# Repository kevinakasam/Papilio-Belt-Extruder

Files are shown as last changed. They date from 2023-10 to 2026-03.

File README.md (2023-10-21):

# Papilio-Belt-Extruder



#### I recommend visiting my website for slightly more aesthetic documentation :)

## A Belt-Extruder, what is that?

No metal teeth biting the filament, but soft rubber belts pushing the filament down to the nozzle. This is the concept of the Papilio: A Belt Extruder which uses regular rubber timing belts instead of metal extruder gears to feed the filament.

You may wonder why we need an extruder that uses belts instead of gears? Guess it’s fair to say, that we all know the woodpattern on flat surfaces or the small bites on the filament when the metal gears grab the filament. With the belts there are no metal teeth damaging the filament, but soft rubber belts pressing against the filament guiding it all the way through the extruder into the nozzle. As all my projects the Papilio is an 100% opensource project.

 

## How does it work?

Powered by a Nema 14 the Papilio uses a gear reduction to drive two tiny 2GT looped timing belts. In order to keep everything as minimalistic and cheap as possible the Papilio uses very common hardware in combination with some printed parts. The Nema 14 doesn’t make it only super compact but also very light weight – only 140g!

The Papilio uses a Dual-Drive System so the filament gets pushed on both sides by the two timing belts. Using some special shaped pulleys the belts get curved and can perfectly warp around the filament. This ensures a maximum contact to the filament for a very strong grip and keep the filament centered.

## There are two of them?

Yes indeed! There are two versions of the extruder, the Papilio and Papilio Lite. After many many iterations the Papilio was the first working version of the belt extruder. The design reminded me on a butterfly so I named the extruder Papilio– latin for butterfly. But I didn’t stop! My goal was to develop a much more powerful design, so I went further into the rabbit hole. After many attempts and failures I ended up with the Papilio Lite: Less weight, more power. This doesn’t mean the original Papilio is outdated, he just got a brother.

 

## What has changed?

### The Papilio Lite

The Papilio Lite got it’s name from the it’s internals – rather than using the BMG Drive Gear assembly, the Lite uses the Gears from the LGX Lite. With the two stage reduction of 44:10 and 37:17 ( or 44:8, 37:17 with a 8T motor) the Papilio Lite is not only much stronger but also lighter! With 130g the Lite saves you another 10g on the toolhead compared to the original Papilio!

The Papilio Lite also uses a Dual-Drive System to feed the filament on both sides by the two timing belts. The much more closed design of the Papilio Lite allows you to print flexibles, which wasn’t possible with the original design.

Like the original Papilio, the Papilio Lite uses the Sherpa Mini footprint, making it compatible with a wide range of toolheads – due to it’s increased depth it got some additional mounting points lining up with the LGX Lite. The boxed and compact design makes it even compatible with the Voron Steathburner!



## Open source - this is our project!

As all my work the Papilio is also an Open Source project - all files are free to use! You get all the STLs and CAD files via my GitHub and the build logs below. I also added a User Mod Folder to the GitHub so you can contribute to the project with your awesome ideas and adaptions. I can't wait to see what you will come up with :) This extruder deserves it to be something special!

Also the CAD file is 100% parametric, so small adaptions like tolerances, different bearing or heatinserts sizes etc. are easy to do! I tried my best to describe the parameters, if you still have any questions feel free to ask. Ah and if you can't do CAD yourself, I'm sure I can help you out ;)



### ❤️ Support my work

All my work is 100% Open-Source and free for everyone to use. But designing and developing all these things takes a lot of time and effort, so if you appreciate my work and would like to support it and also help cover the costs of gettings the mods perfect, you can use one of the following links. Thanks a lot 🤍

<a href="https://www.buymeacoffee.com/kevinakasam" target="_blank">Buy Me A Coffee</a>


## How can I try this out?

### Current state: Beta-Testing

After seven months of a closed Alpha Testing it's time for a public Beta!

While we did a lot of testing and improving during the Alpha, there's still room for improvements. If the Papilio caught your interest you can now build your very own Papilio extruder! As for all my Beta testings all communication will happen on my Discord - check the channel "#papilio-chat" for more information. All files are available on my GitHub - check the build instructions below. 
Click on the icon to join my [Discord Server](https://discord.gg/xqpKrxt9FC):

<a href="https://discord.gg/xqpKrxt9FC">
         <img alt="Join" src="https://github.com/kevinakasam/BeltDrivenEnder3/blob/main/_ignore/Pictures/Discord-Logo%2BWordmark-Color.png"
         width=250" >
      </a>

### Alpha Testing: Completed

You are awesome! After half a year of Alpha testing we can now start the public Beta. Thank you very very much for all your help, suggestions, time and willing to help.  Shoutout to these awesome people:

You | are | some | really | awesome | People!!
:-------------------------: | :-------------------------: | :-------------------------: | :-------------------------: | :-------------------------: | :-------------------------:
 |   |   |   |   |      
1957Axel | 10Boltoa | aid3nn | André | Andy | barnus84
bigbosshogg412 | Bomble_doodle | Butter202 | Chilly | chestwood96 | [CR3D](https://www.cr3d.de/)
Ciccius | diabolicaldan | Farva | Fruitz | hawk16zz | interitus
JamesH | Keh | Kingn00dles | Lemcott | Luigivaba | macuser_1984
memy | Mr ed | Naraki | [oldcrazyeye/CrazyLlamaCustoms](https://github.com/oldcrazyeye) | oliof | PCR
Phanzer | PigeonGiraffe | pnewb | q66 | qwib | SpitefulOwl
Stu | tcbp | Tkaus | verm | Wight555 | [zruncho](https://github.com/zruncho3d)

## Build Instructions

I'm glad that you want to give the Papilio a try. Just click on the Papilio you want to build:

<a href="https://kevinakasam.com/papilio-build-instructions/">
         Click
      </a>

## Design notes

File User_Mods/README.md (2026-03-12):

# User Mods

This respository is to share your Mods (Mods of my Mods are called Mods in the following). You can add them by submitting a pullrequest.
All my Mods have a sperate folder, that may include further subfolders, please sort your content as described below:

## Table structure

*Thanks to the [Voron_User](https://github.com/VoronDesign/VoronUsers) Repo for this table shematic! 
Update the following table with the information about your mod:
- Your name
- A link to your sub-folder
- A short description of your mod
- The extruder compatibility. Use `:heavy_check_mark:` for :heavy_check_mark:,`:x:` for :x: and `:grey_question:` for :grey_question:

like so:
`
| Creator | [Mod title](link) | Description | :x: | :x: |`

| Creator | Mod title | Description | Papilio | Papilio Lite |
| --- | --- | --- | --- | --- |
| KevinAkaSam |[XOL2_Mounts](./KevinAkaSam/XOL2_Mounts)| XOL2 Mounts for the Papilio (Lite) including Tap  | :heavy_check_mark: | :heavy_check_mark: |
|  |[Stealthburner_Mount](./KevinAkaSam/Stealthburner_Mount)| Stealthburner Mount for the Papilio Lite  | :x: | :heavy_check_mark: |
| adamstorm | [Filament Sensors](./adamstorm/Filament%20Sensors) | Top Cover with filament sensors | :x: | :heavy_check_mark: |
| cobre | [A4T Extruder Adapters](./cobre/A4T%20Extruder%20Adapters) | Adapter to use Papilio extruder with A4T toolhead | :grey_question: | :heavy_check_mark: |
| hawk16zz | [PapLite Combo Mount](./hawk16zz/Combo_SM_LGX_lite_for_Frank2.0) | Extra mounting options for the PapLite with Frank2.0 | :x: | :heavy_check_mark: |
|  | [PapLite Strain Relief](./hawk16zz/Mountable_LGX_Lite_strain_relief) | Cable Strain Relief Bracket for PapLite | :x: | :heavy_check_mark: |
|  | [PapLite Front EBB36](./hawk16zz/Front_EBB36_PapLite) | Mount to attach a EBB36 to the Front of the PapLite | :x: | :heavy_check_mark: |
| n4t3 | [Papilio Top Cover HGX Collet](./n4t3/Papilio_HGX_Collet) | Top Cover to attach HGX Collet to top | :x: | :heavy_check_mark: |
|  | [Papilio Top Cover M6 Bowden Dual](./n4t3/Papilio_M6_Bowden_Dual) | Top Cover to attach M6 Bowden Coupler to top and bottom | :x: | :heavy_check_mark: |
|  | [Papilio Top Cover M6 Bowden](./n4t3/Papilio_M6_Bowden) | Top Cover to attach M6 Bowden Coupler to top | :x: | :heavy_check_mark: |
| theFPVgeek | [FlexiPap](./theFPVgeek/FlexiPap) | Modified Papilio Lite TPU Cover and HGX 1.x geared Upper Base for <95A flexible filaments | :x: | :heavy_check_mark: |

## How to create a pull request 

1. Create a fork of the respository
    - You can find a Button labeled `Fork` at the top right. Clinking on that creates a copy aka fork of this respository in your GitHub account.

2. Create a new folder
    - Navigate into the Mod folder you want to upload your Mod to.
    - Click on `Add file` -> `Create new file`. Then type `YourNickname/YourModName/README.md` to create your folder (click on `commit new file`).
    - If you plan to upload more than one Mod, add simply add more subfolders in your folder like `YourNickname/YourFirstModName/README.md` and `YourNickname/YourSecondModName/README.md` and so on. 
    - Please use short folder names.

3. Edit README and add your files
    - Click on the README.md and then on the pencil on the right top/center to edit the README. Add all required information as described below.
    - Click on `Add file` -> `Upload files` to upload all your Mod files.
    - The stock title of a commit is `Add files via upload` replace that with the title of your Mod.

4. Edit the main README.md of the Mod
    - Navigate back to the Mod folder you made your Mod for. Edit this file and add your mod to the alphabetic table by adding a new line with `| Creator | [Mod title](link) | Description | | :x: | :x: |`
    - The `link` for the `[Mod title](link)` should look like that: `./YourNickname/YourModName` just like you did above
    - Example: `| KevinAkaSam | [Modifius](./KevinAkaSam/Modifius) | Modifius adds ...  | :grey_question: | :grey_question: |`
    - Note `Modifius` is just an idea, yours may be called `Adaption to bearing size xy`

5. Submit the Pullrequest
    - Navigate back to this respository (not the one you forked) and click on `Pull requests` next to `<> Code` `© Issues`
    - Click on the green square on the right `New pull request`
    - A new dialog/window opens and starts with:
        >Compare changes
        >
        >Compare changes across branches, commits, tags, and more below. If you need to, you can also `compare across forks`.
    - Click on the `compare across forks` and at the line below select your forked respository as `head respository`
    - Add you Mod name as title of the pullrequest, add the information to the form and click on  `Create Pull Request` at the very end.
    - If you did anything right we will merge your pullrequest :)
 
## Create a folder

To add your work create a folder that has the following structure:

    - Main respository `User-Mods` 
        - Nickname Subfolder eg. `KevinAkaSam`
            - Modname Subfolder eg. `Modifius`
            - Modname Subfolder eg. `Modimedi`
        - Nickname Subfolder eg. `SamAkaKevin`
            - Modname Subfolder eg. `Mod_A`
            - Modname Subfolder eg. `Mod_B`

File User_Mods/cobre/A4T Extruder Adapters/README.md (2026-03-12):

# A4T Papilio Extruder Adapter

A new toolhead that seems to be gaining popularity is [Armchair Engineering's A4T](https://github.com/Armchair-Heavy-Industries/A4T/). I decided I was going to try it out, but I realized that my extruder wasn't going to fit. I recently switched to [KevinAkaSam's Papilio Lite](https://kevinakasam.com/papilio/) extruder, and while it uses the same mounting holes as Sherpa Mini (Which A4T supports without an extruder adapter), the stepper motor on the rear won't clear the toolhead cowl.

I remixed the included adapter for LGX Lite, and made versions for both XOL and CW2/Tap carriages. 

I have not tested this with Papilio non-lite, but I don't see why it wouldn't work

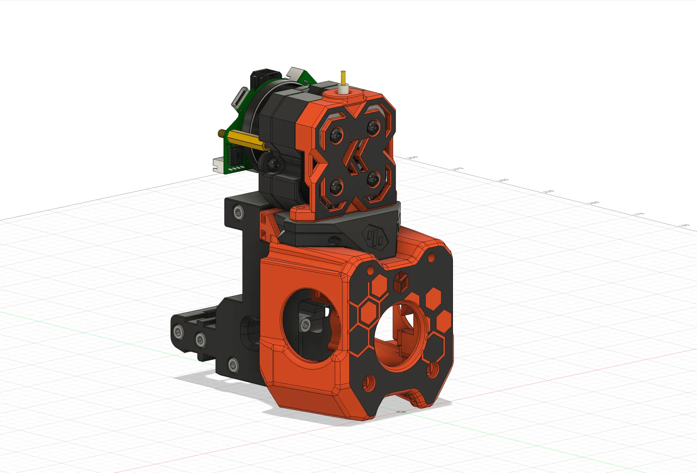
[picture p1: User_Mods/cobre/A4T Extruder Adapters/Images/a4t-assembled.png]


There are versions for both XOL and CW2/Tap carriages, and each has a variant with or without the Voron logo

<br>

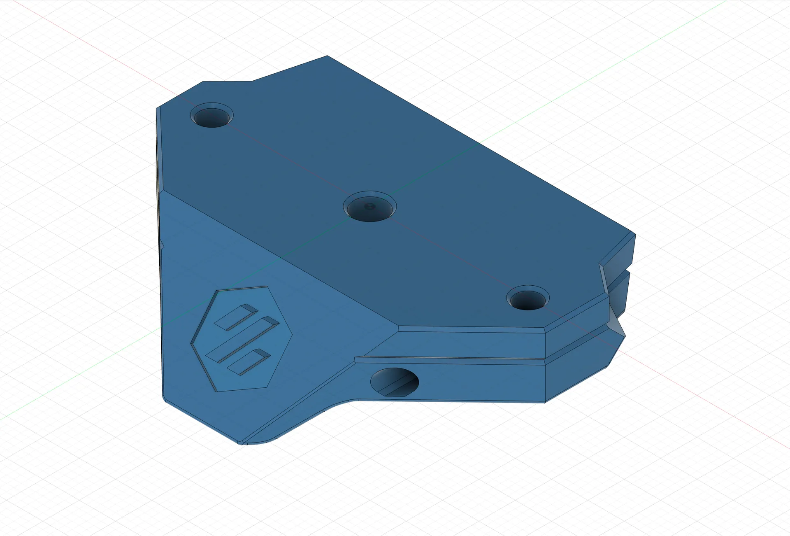
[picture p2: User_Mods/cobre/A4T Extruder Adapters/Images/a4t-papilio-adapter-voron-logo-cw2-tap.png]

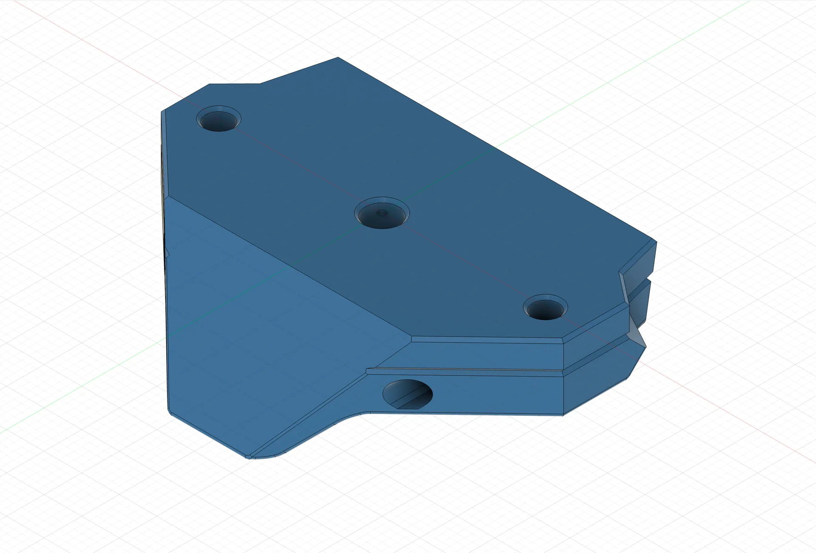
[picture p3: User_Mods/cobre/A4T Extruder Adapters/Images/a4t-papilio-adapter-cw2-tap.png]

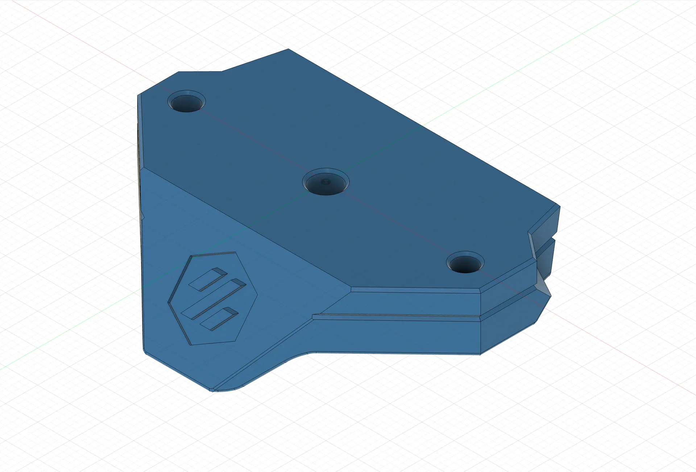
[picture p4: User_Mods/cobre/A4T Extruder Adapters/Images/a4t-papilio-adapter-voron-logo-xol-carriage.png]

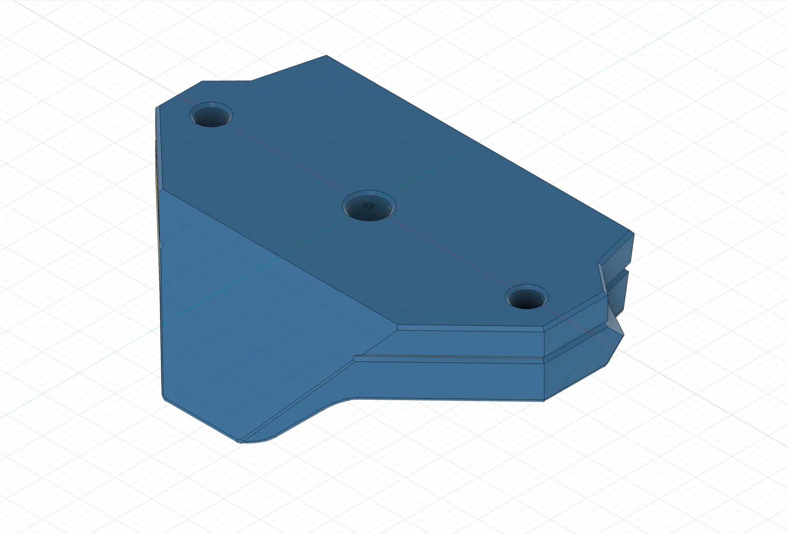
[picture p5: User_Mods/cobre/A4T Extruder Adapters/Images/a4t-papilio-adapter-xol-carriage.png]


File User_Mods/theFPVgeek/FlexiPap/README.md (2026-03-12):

I created another top cover for flexible filaments after attempting to use the available TPU-specific cover. Unfortunately, anything softer than 95A shore filament would still jam the filament. After some testing, I tightened the tolerances at the cover and the upper base. With these modified parts, I've been able to print as soft as both 85A Ninjtek NinjaFlex TPU and 75A NinjaTek Chinchilla TPE.

Versions Available:
- Top Cover with Standard logo -- TopCover-FlexiPap-ver4F
- Top Cover with No Log -- TopCover-for-Flexibles-CLEAR-ver4F
- Top Cover with Voron logo -- TopCover-for-Flexibles-ver4F-VORON
- Upperbase (HGX v1.x gears) -- (BaseUpper_HGX-ver4.)
- Upperbase (HGX v1.x gears) w/mounting tab for Anthead toolhead -- (BaseUpper_HGX-ver4-AntHead_Mount)

papdbmod





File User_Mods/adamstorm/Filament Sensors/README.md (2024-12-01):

Add filament sensors to your Pap lite extruder! 

Two different configurations
- Single Sensor has a pre-extruder gear sensor
- Dual Sensor has the same sensor above the gears, but also one below the gears.

While the single sensor version has a bit of a [Doug Dimmadome](https://www.google.com/search?q=doug+dimmadome) vibe, the dual sensor is downright hideous looking. Looks aren't everything though, and these both work great! If you are running this with the Frank 2.0 toolhead, there is an [extruder mount](https://github.com/kevinakasam/FrankEnstein-Duct/tree/main/User%20Mods/adamstorm/Filament%20Sensor) that has a post-gear sensor so you can use the less-obnoxious single sensor version here. 

Both configurations come with either the standard or TPU top cover profile from the r3 pap lite release, and both profiles have versions of solid or cut faces. 

The top sensor is positioned at an angle to allow access to the 3rd mounting point of the pap lite extruder. This switch should be installed once the extruder is fastened in place due to the switch blocking the mounting point access hole. 

BOM:
- D2F microswitch (or similar), doesn't need to be super accurate - we're not setting z-position here
- 5.5mm ball bearing (example: https://a.co/d/6RdxncY or https://a.co/d/gXpXHlg)
- M2x8 self-tapping screws (2x)
- ECAS04 fitting (remove rubber stopper from the bottom, it's not needed)

Wiring is a little tight. I had to trim the legs of the bottom switch down to get it to fit well.

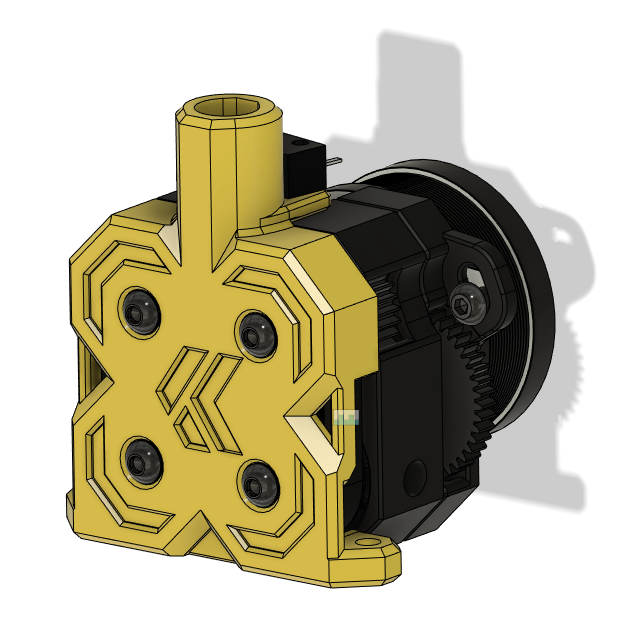
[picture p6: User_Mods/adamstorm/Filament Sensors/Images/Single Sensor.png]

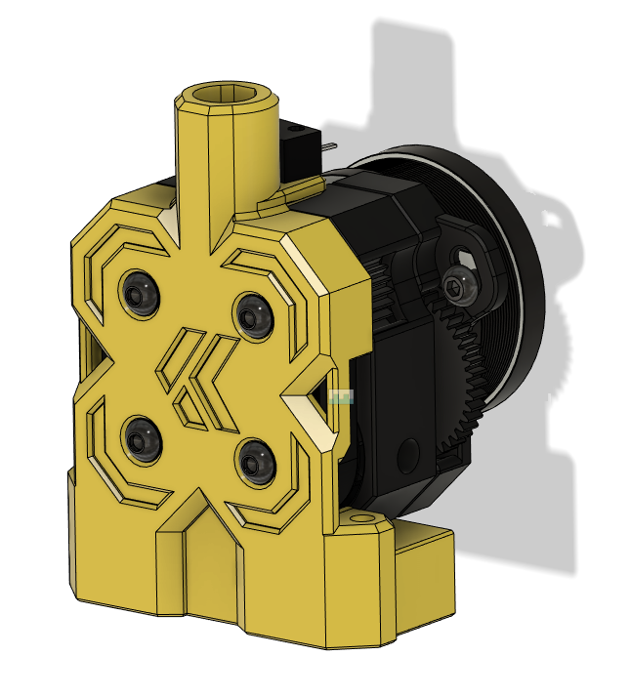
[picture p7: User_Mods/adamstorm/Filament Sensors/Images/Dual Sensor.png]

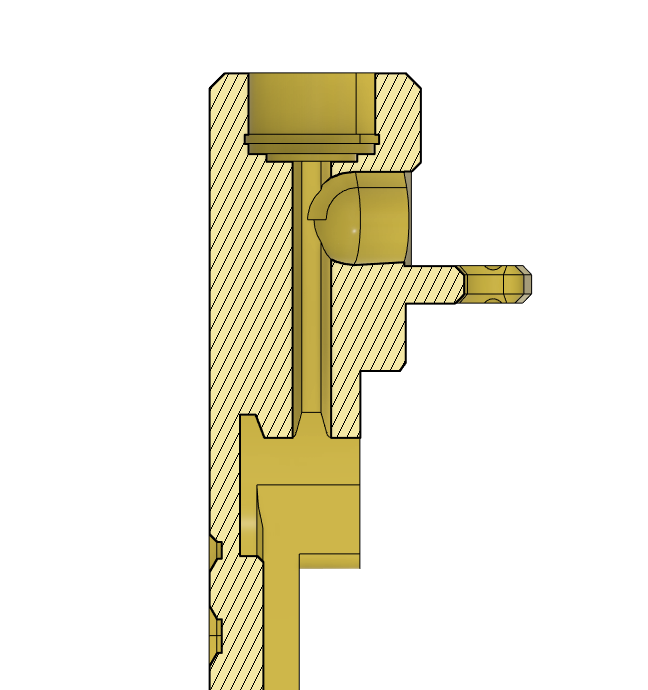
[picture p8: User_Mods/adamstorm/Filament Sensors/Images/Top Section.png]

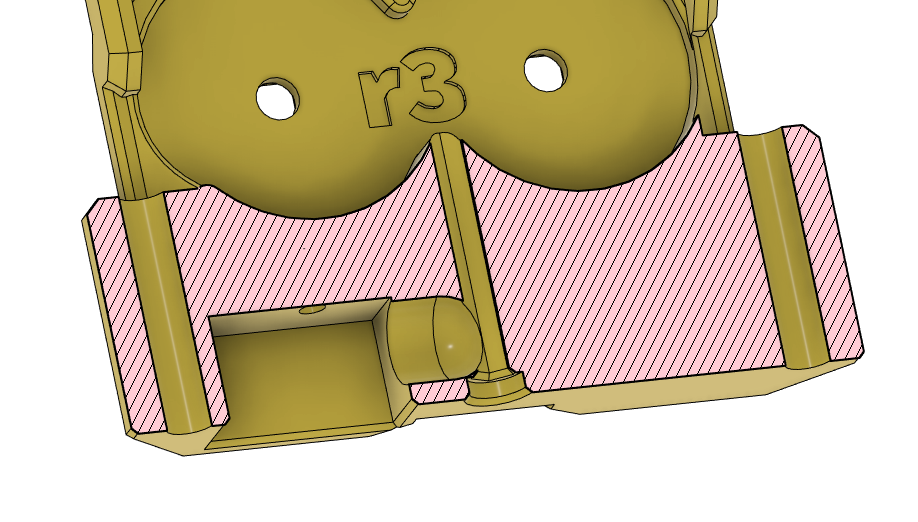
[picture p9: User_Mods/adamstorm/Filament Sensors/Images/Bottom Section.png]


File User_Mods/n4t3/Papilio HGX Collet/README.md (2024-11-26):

This front plate allows the collet that comes with the HGX Lite kit to be added at the top as a retainer for the bowden tube. Using a soldering iron, heat the metal ring and seat it in the top so that the end is either flush with the top face or just a bit higher, then insert the plastic retainer. **If the ring is inserted too far, there will not be enough space for the blue plastic lock ring.**

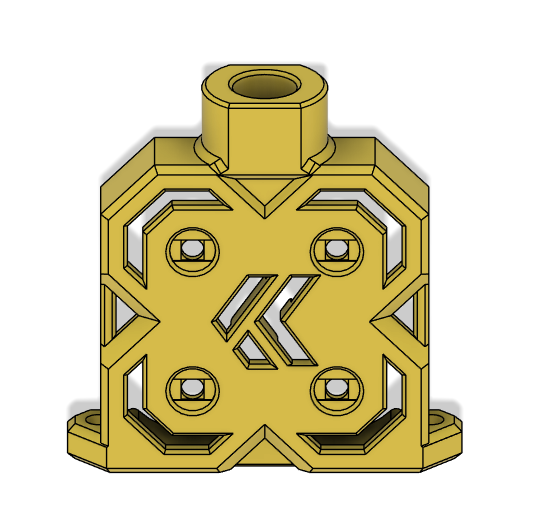
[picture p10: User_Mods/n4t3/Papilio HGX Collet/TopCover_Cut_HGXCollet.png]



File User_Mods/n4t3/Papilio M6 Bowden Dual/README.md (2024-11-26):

This front plate allows a M6 Bowden coupler to be added at the top and bottom of the extruder. This is useful for bowden setups with a reverse bowden tube. The M6 coupler can screw directly into the plastic.

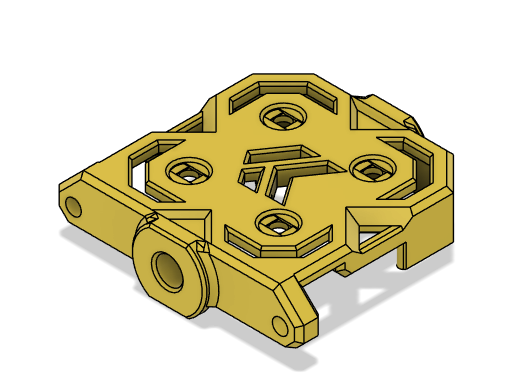
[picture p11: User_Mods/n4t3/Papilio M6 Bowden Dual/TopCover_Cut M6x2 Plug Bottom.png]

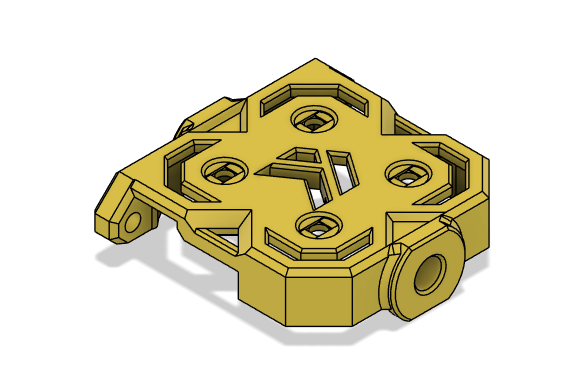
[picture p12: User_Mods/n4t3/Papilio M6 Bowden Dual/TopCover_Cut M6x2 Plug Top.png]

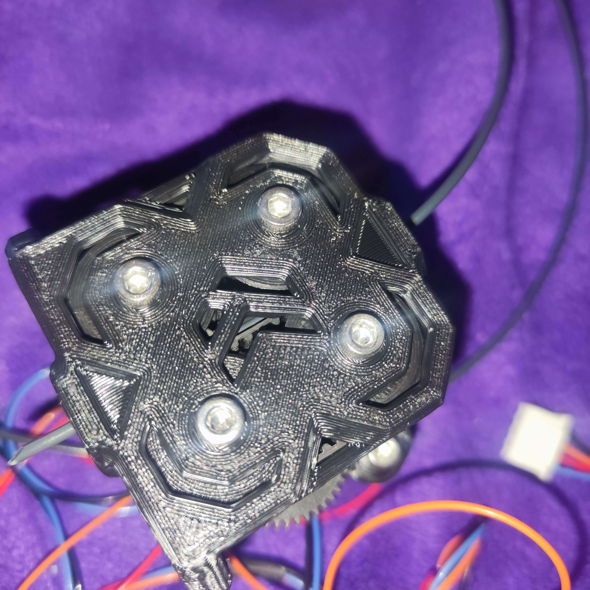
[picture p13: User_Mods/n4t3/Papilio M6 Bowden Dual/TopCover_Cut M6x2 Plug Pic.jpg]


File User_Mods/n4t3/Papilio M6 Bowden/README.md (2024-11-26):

This front plate allows a M6 Bowden coupler to be added at the top of the extruder. The M6 coupler can screw directly into the plastic.

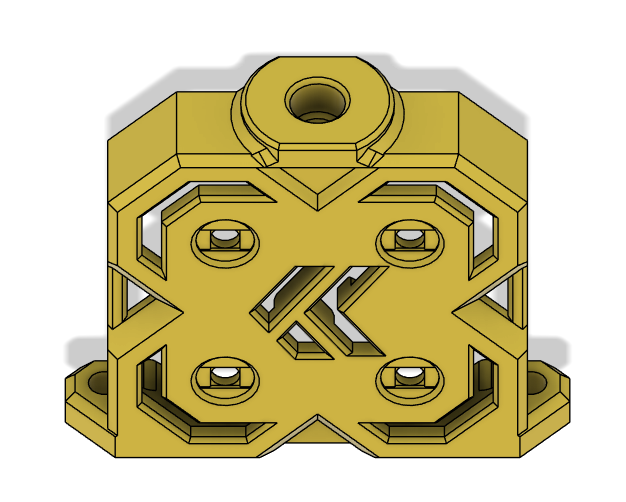
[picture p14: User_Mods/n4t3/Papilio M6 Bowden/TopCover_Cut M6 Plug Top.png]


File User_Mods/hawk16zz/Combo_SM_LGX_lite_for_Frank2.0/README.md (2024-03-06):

An extruder mount that adds the back two LGX lite mounting holes to the Sherpa mini mount of the [FrankEnstein Duct 2.0](https://github.com/kevinakasam/FrankEnstein-Duct/tree/main/Frank2.0_Beta) for the PapLite with the additional LGX mounting. Also a new version for the the PapLite R3.

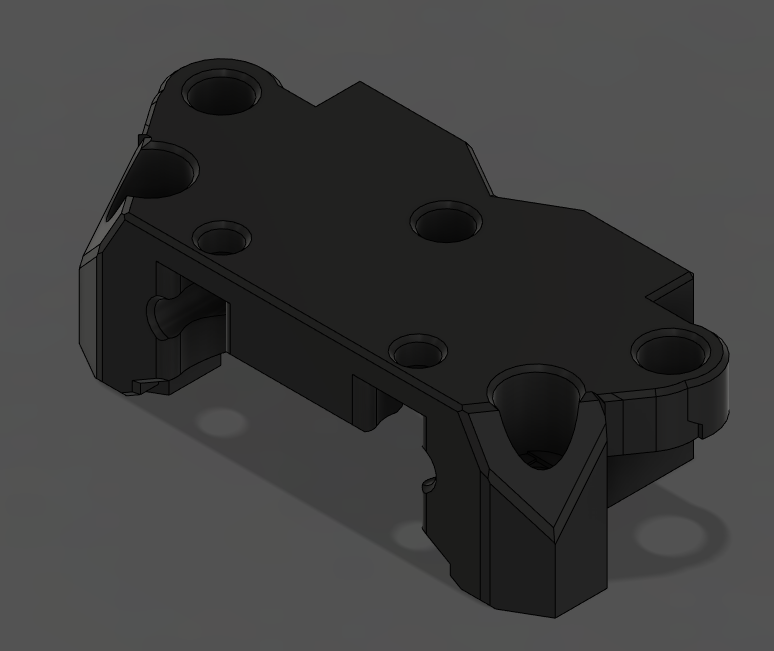
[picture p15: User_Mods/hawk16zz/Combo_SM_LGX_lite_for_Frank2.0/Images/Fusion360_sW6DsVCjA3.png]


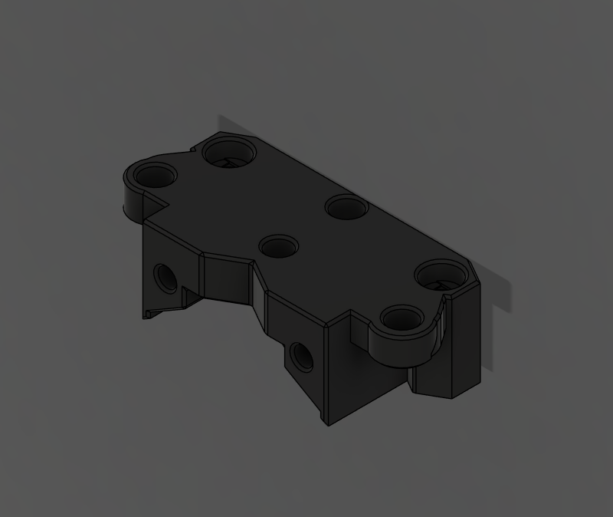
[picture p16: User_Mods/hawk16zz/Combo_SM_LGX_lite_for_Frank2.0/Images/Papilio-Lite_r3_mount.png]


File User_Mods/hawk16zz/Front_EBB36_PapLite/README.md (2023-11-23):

A front faceing mount for a EBB36 or similar for the Papilio Lite. You will need to replace the M3x20mm cover screws with M3x25mm BHCS to mount the mount to the PaplLite, 2 M3x4x5mm, and 2 M3x4mm or M3x6mm to secure the board to the mount.

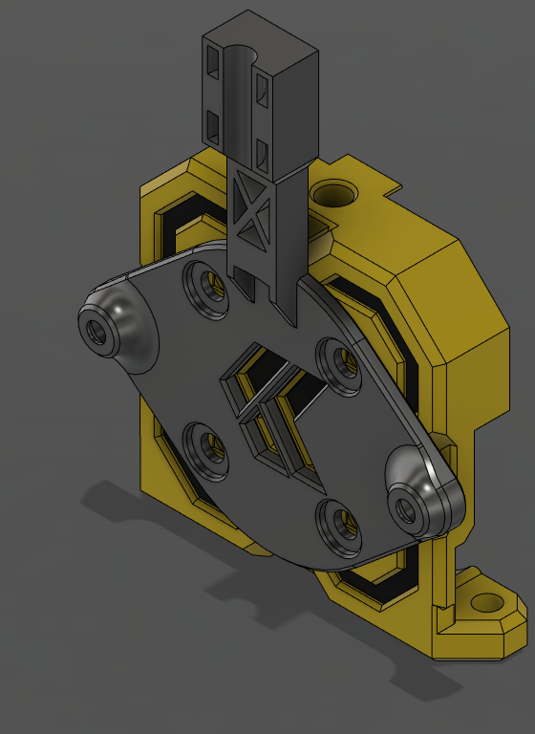
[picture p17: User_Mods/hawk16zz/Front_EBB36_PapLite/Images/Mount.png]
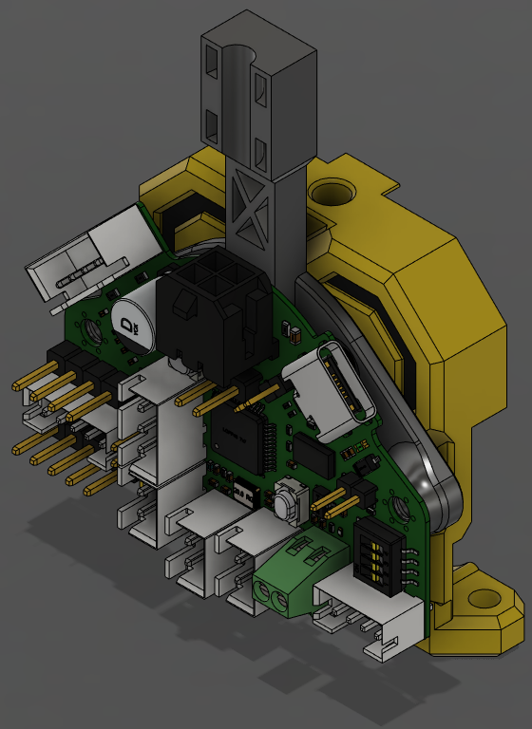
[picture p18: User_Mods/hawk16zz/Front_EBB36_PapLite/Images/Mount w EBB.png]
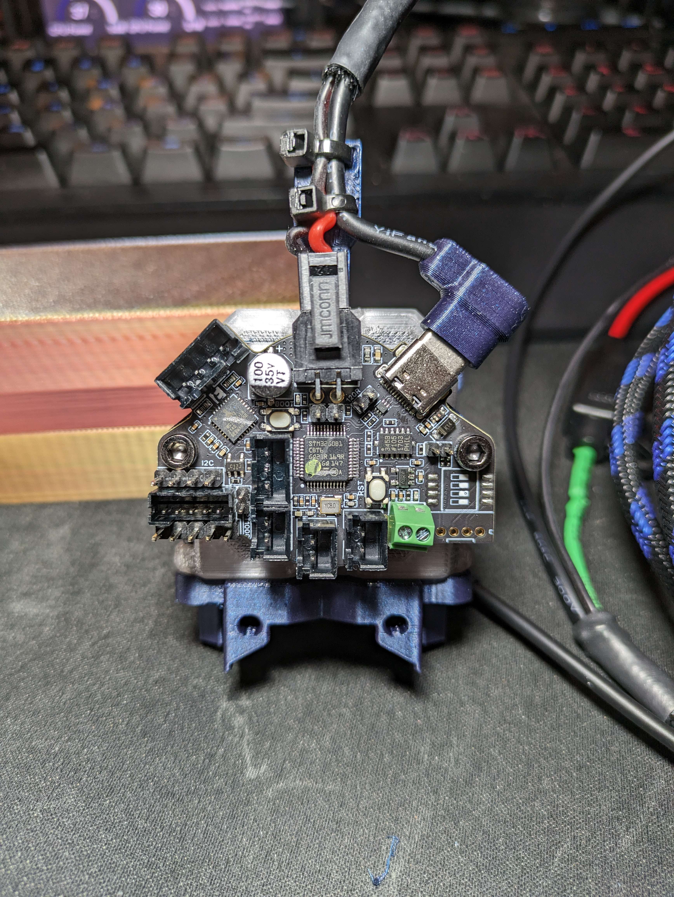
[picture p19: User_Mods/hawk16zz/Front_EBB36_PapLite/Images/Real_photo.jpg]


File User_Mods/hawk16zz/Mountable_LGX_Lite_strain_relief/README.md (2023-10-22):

A strain relief bracket that mounts to the side LGX lite holes of the extra housing for the PapLite

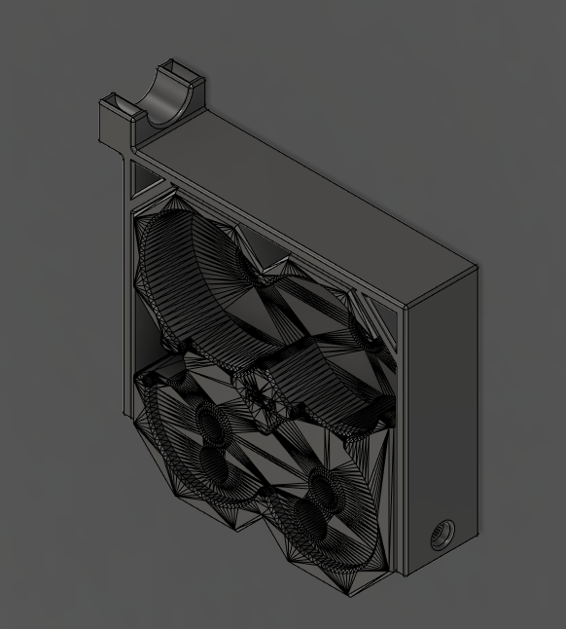
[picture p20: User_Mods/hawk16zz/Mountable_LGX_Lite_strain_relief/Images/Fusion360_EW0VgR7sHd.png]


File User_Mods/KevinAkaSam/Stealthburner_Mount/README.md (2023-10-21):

# Voron Stealthburner Mount for the Papilio Lite

This is a modified CW2 mount to mount the Papilio Lite (The OG Pap does not fit!) on the [Voron Stealthburner](https://github.com/VoronDesign/Voron-Stealthburner). It's modified from the [LGX Lite](https://github.com/Eytecz/LGX_Lite_Stealthburner_CW2_style_mount) SB Mount. Thank's a lot for the CAD! 



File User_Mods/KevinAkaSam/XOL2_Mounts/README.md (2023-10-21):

# XOL2 Mount for the Papilio

Pretty much self explaining. These are some slightly modified [Shera Mini](https://github.com/Annex-Engineering/Sherpa_Mini-Extruder) mounts from/for the [XOL2](https://github.com/Armchair-Engineering/Xol-Toolhead) (they're raised by 4mm).

Since I'm using an older version of XOL2 I havent tested these exact files. So please do a test fit before disassembling anything and report back if this fits or if there are any issues.



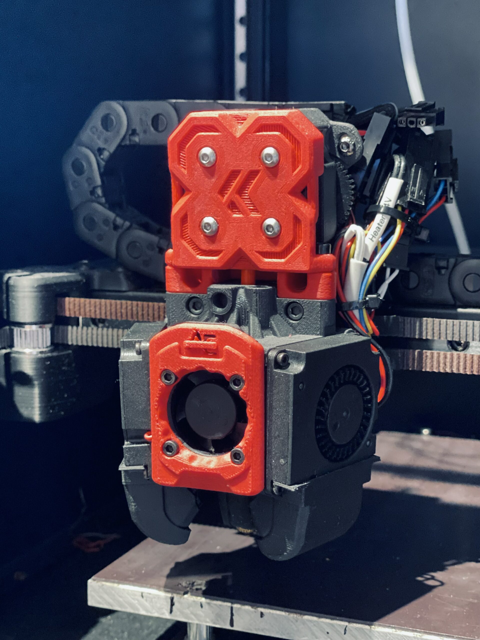
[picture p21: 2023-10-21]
User_Mods/KevinAkaSam/XOL2_Mounts/Images/Pap_Xol.jpg

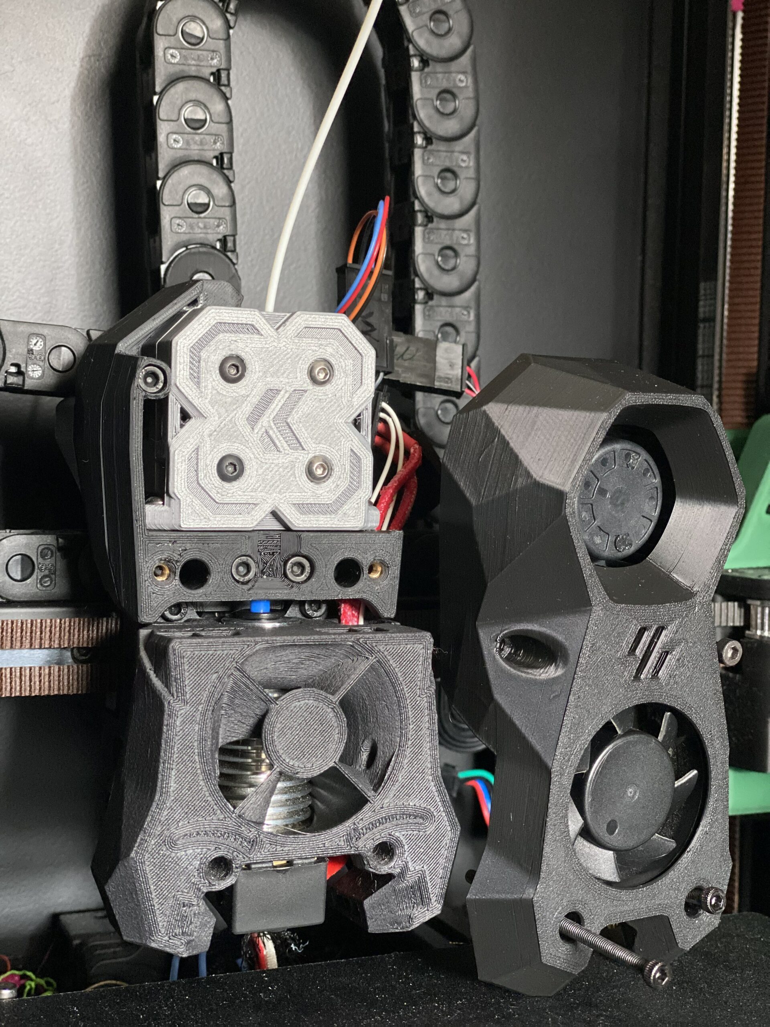
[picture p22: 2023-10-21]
User_Mods/KevinAkaSam/Stealthburner_Mount/Images/Pap_SB.jpg

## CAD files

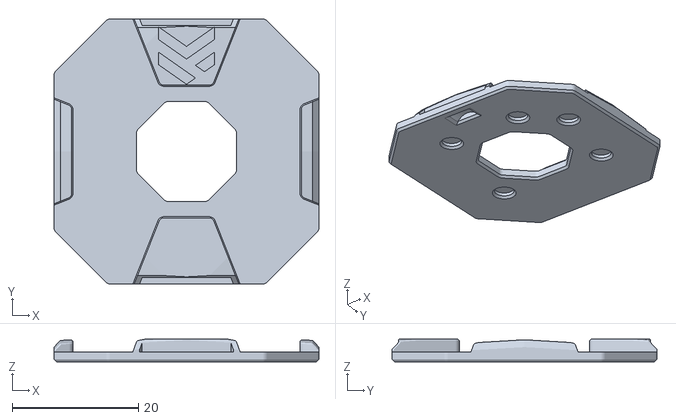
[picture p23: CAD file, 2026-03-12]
Papilio Legend/STL/Faceplate_Main.stl
42.0 x 42.0 x 3.60

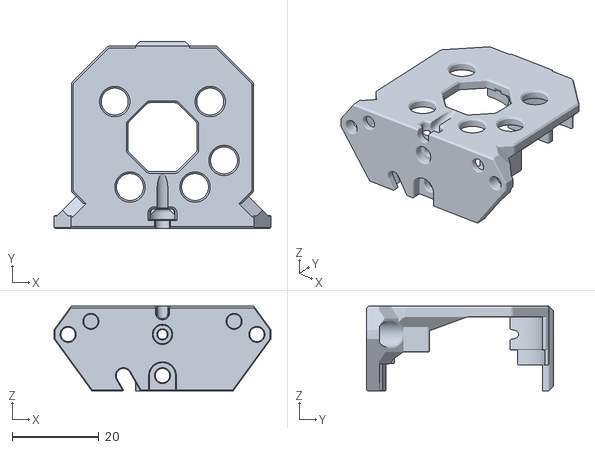
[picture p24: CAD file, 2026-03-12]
Papilio Legend/STL/TopShell.stl
50.0 x 43.0 x 19.5

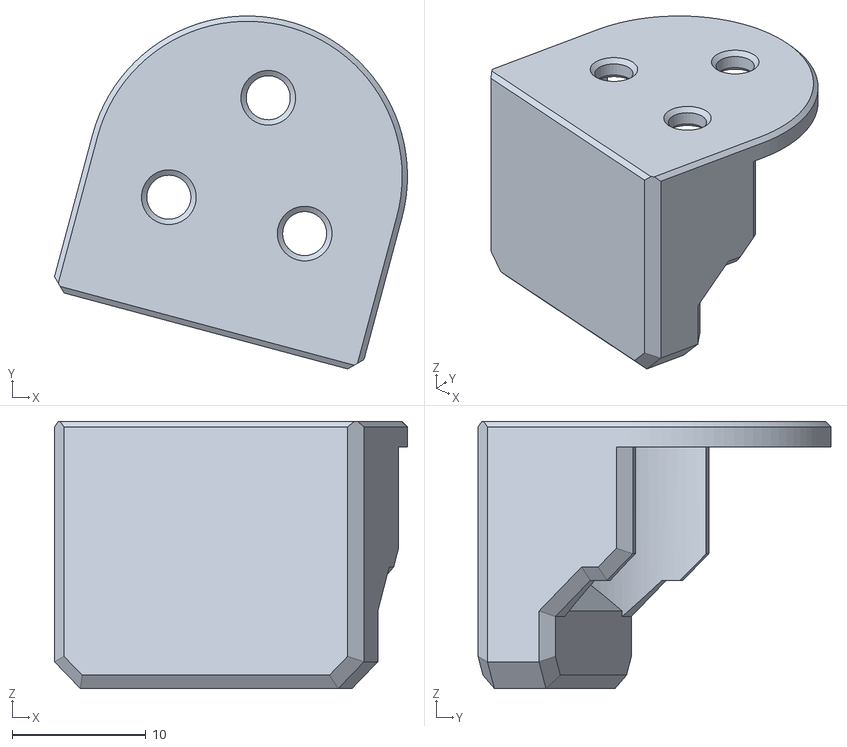
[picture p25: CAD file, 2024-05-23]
Papilio Lite/_Ignore/HGX2.0xTBG/Cut_Guide.stl
26.4 x 26.4 x 20.0

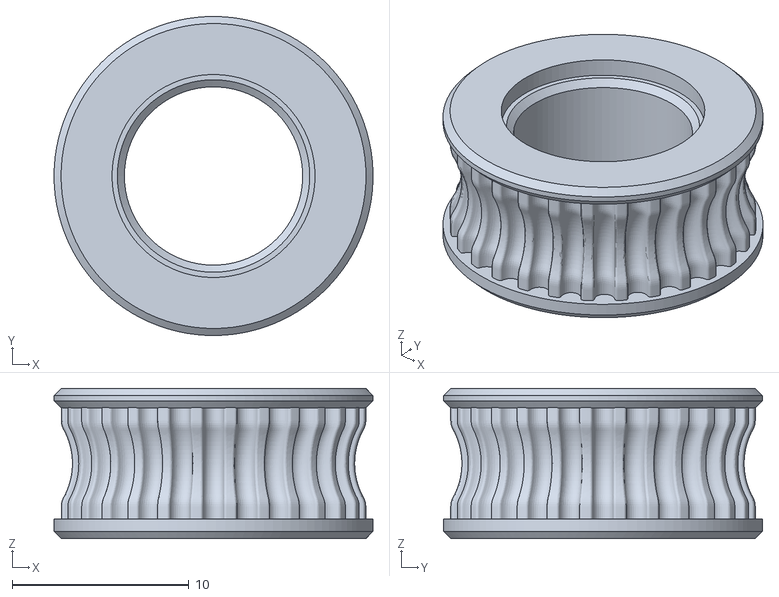
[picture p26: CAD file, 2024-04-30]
Papilio Lite/Common/2x_Idler_Pulley_F623_r3.1.stl
18.1 x 18.1 x 8.50

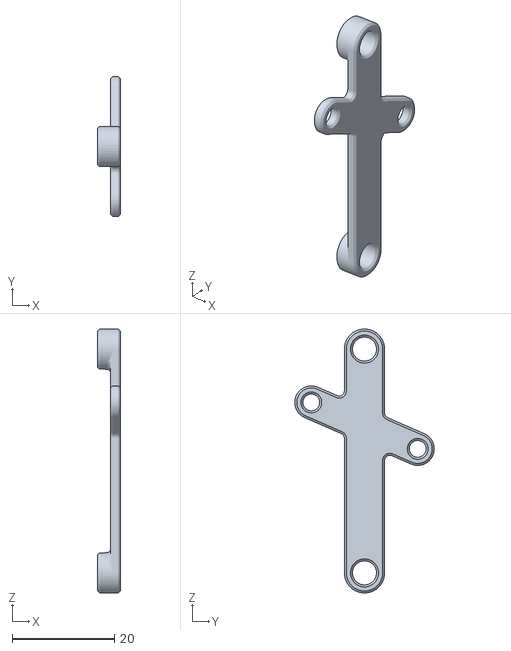
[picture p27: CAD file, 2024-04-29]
Papilio Lite/Common/PCB/36mm_SIde_Spacer.stl
4.50 x 27.3 x 51.7

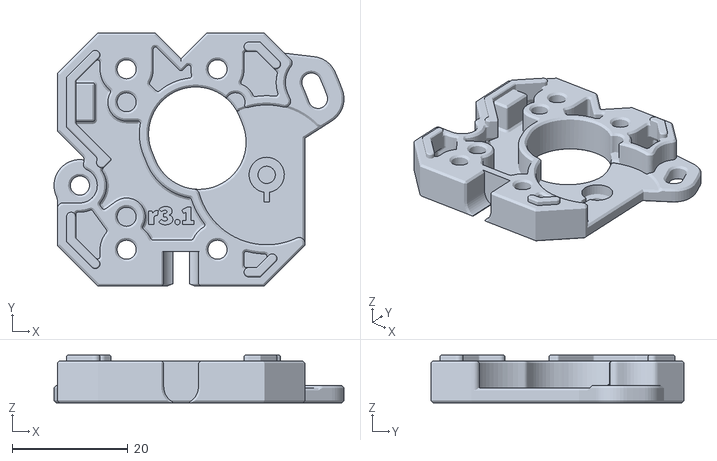
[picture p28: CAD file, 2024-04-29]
Papilio Lite/HGX/BaseLower_r3.1.stl
50.2 x 43.8 x 8.30

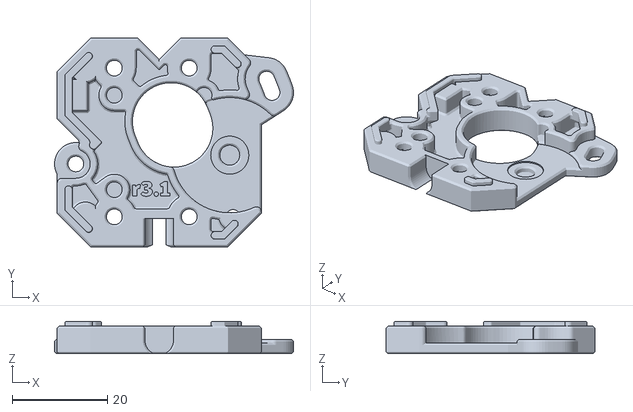
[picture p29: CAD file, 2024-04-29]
Papilio Lite/LGX/BaseLower_r3.1_PCB.stl
50.2 x 43.8 x 6.80

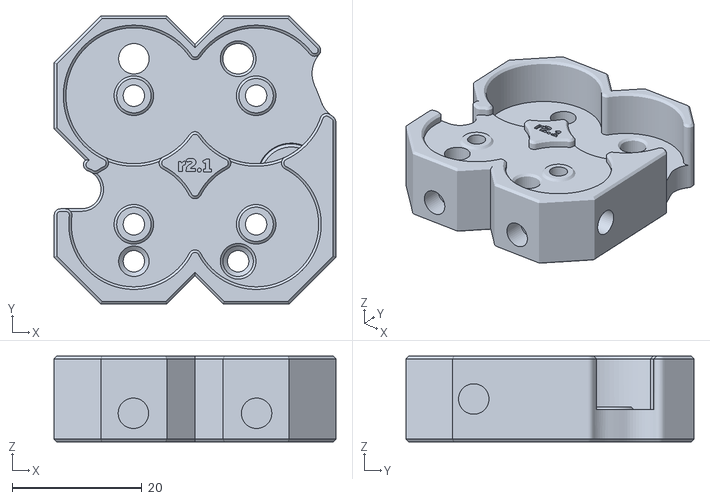
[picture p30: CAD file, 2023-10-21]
Papilio Lite/STL/Extras/LGX_Lite_Mounting/BaseUpper_LGX_Lite_Mounting_r2.1.stl
43.4 x 44.4 x 13.2

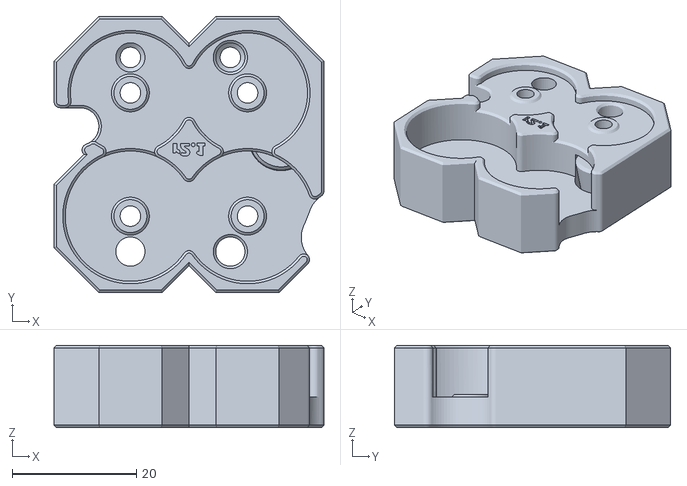
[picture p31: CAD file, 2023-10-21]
Papilio Lite/STL/Extras/Mirrored/BaseUpper_Mirror_r2.1.stl
43.4 x 44.4 x 13.2

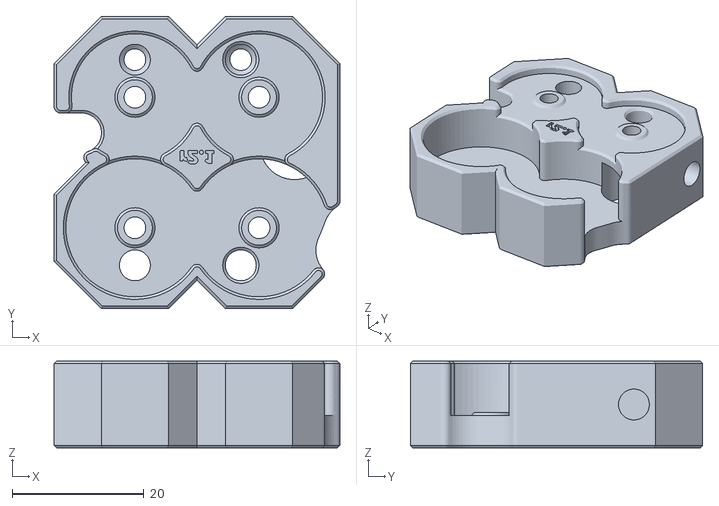
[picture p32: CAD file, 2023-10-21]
Papilio Lite/STL/Extras/Mirrored/LGX_Lite_Mounting/BaseUpper_LGX_Lite_Mounting_Mirror_r2.1.stl
43.4 x 44.4 x 13.2

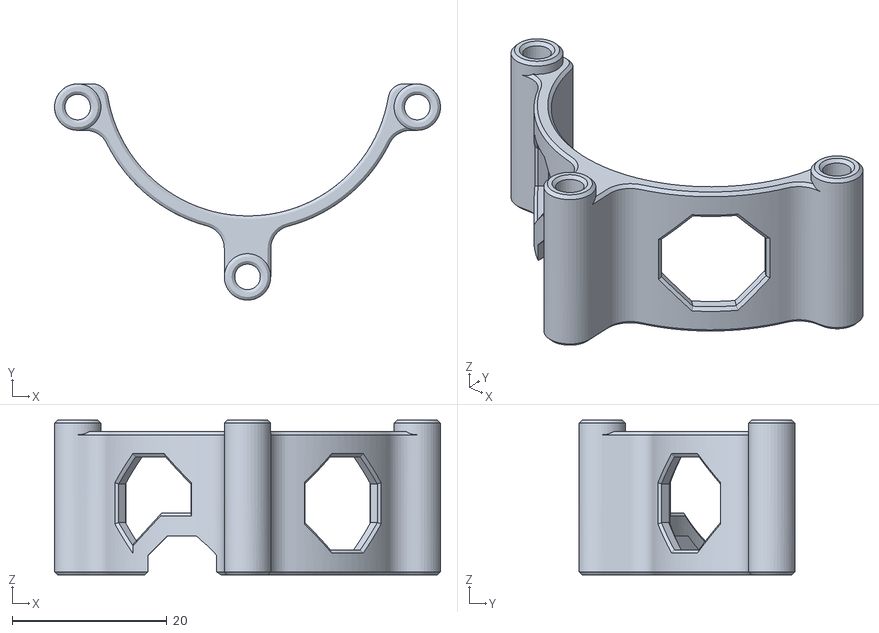
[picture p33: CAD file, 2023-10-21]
Papilio Lite/STL/Extras/Mirrored/PCB_Mounts/42mm_Spacer_Mirror.stl
49.8 x 27.9 x 20.0

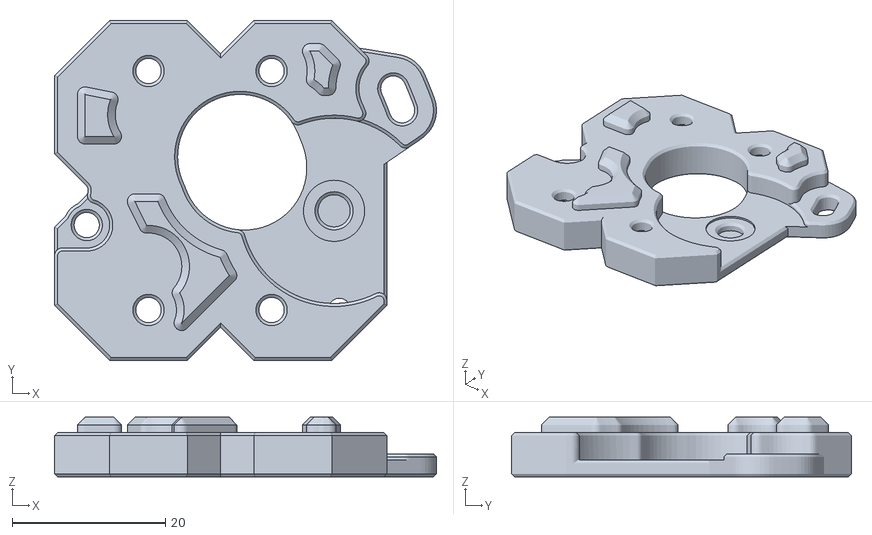
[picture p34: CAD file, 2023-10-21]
Papilio Lite/STL/Extras/PCB_Mounts/BaseLower_PCB_r2.1.stl
49.9 x 44.4 x 7.80

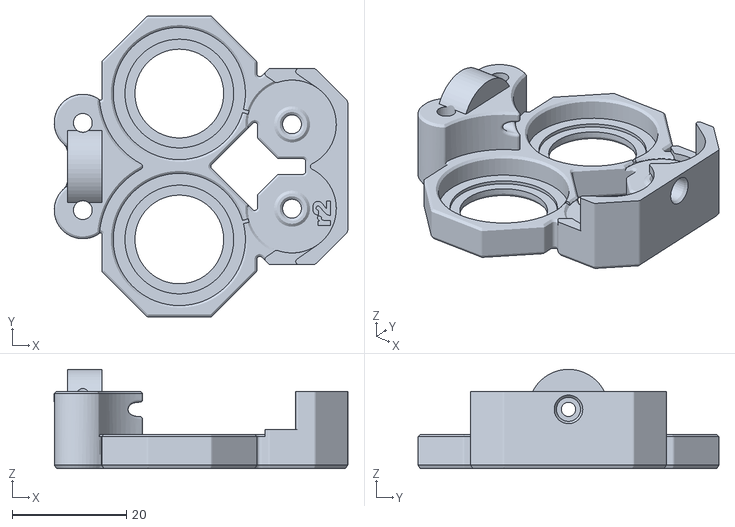
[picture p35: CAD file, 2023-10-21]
Papilio/STL/TopShell_PressFit_r2.stl
51.3 x 52.6 x 17.3

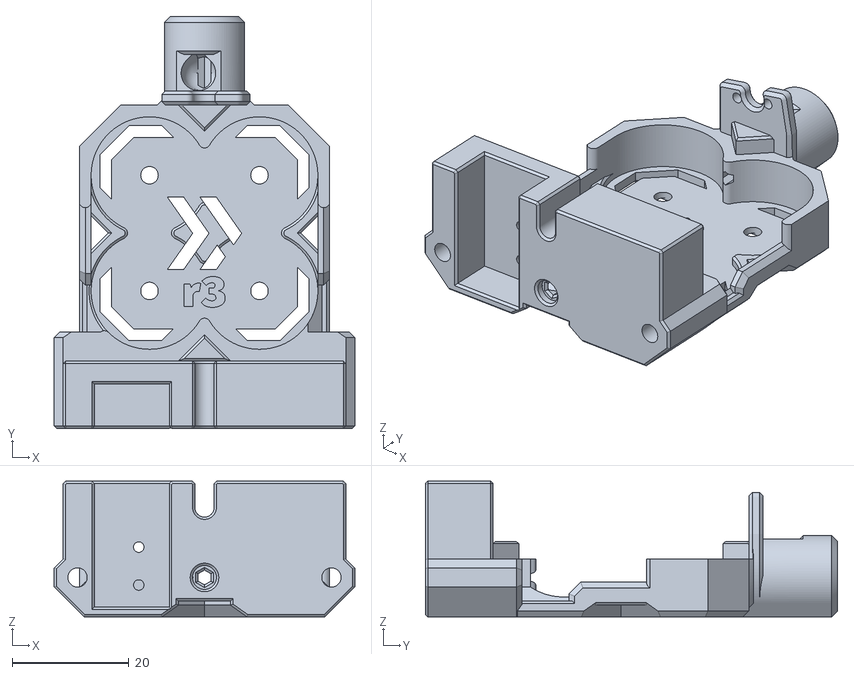
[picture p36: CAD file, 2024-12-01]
User_Mods/adamstorm/Filament Sensors/STL/TopCover Dual Sensor Cut.stl
51.5 x 70.6 x 23.2

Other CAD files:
User_Mods/cobre/A4T Extruder Adapters/STL/a4t-papilio-adapter-voron-logo-xol-carriage.stl
User_Mods/hawk16zz/Combo_SM_LGX_lite_for_Frank2.0/STLs/Frank2 PapLite R3 Mount.stl
User_Mods/hawk16zz/Front_EBB36_PapLite/STLs/Front Toolhead Board.stl
User_Mods/hawk16zz/Mountable_LGX_Lite_strain_relief/STLs/Pap_LGX_Cable_mount.stl
Papilio Legend/STL/Base.stl
Papilio Legend/STL/EBB_36_PG7.stl
Papilio Legend/STL/Faceplate_Accent.stl
Papilio Legend/STL/Faceplate_MMU.stl
Papilio Legend/STL/Faceplate_Ring.stl
Papilio Legend/STL/Middle.stl
Papilio Legend/STL/Spacer.stl
Papilio Lite/Common/2x_Idler_Pulley_r3.1.stl
Papilio Lite/Common/CutGuide_r2.stl
Papilio Lite/Common/OLD/TopCover_r2.1.stl
Papilio Lite/Common/OLD/TopCover_r2.2.stl
Papilio Lite/Common/PCB/36mm_Spacer.stl
Papilio Lite/Common/PCB/42mm_Side_Spacer.stl
Papilio Lite/Common/PCB/42mm_Spacer.stl
Papilio Lite/Common/Pulley_Guide.stl
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

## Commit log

2023-10-21 Initial Release
    [36mm_Spacer.stl, 36mm_Spacer_Mirror.stl, 42mm_Spacer.stl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]
2023-10-21 User Mods fix
    [Cable_cover_Papilio_Lite.stl, Front_body_Papilio_Lite.stl, Rear_body_Papilio_Lite.stl]
2023-10-23 Fixed CAD naming
2023-10-25 Added missing CutGuide.stl
    [CutGuide_r2.stl]
2023-11-03 Removing CAD (temporary)
2023-12-31 Fixed width of front toolhead board...
    ... so M3x25mm BHCS can properly fit
    [Front Toolhead Board.stl]
2024-02-17 Papilio Lite r3 Update
    [36mm_Spacer.stl, 36mm_Spacer_Mirror.stl, 42mm_Spacer.stl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]
2024-02-18 Minor Top Cover PTFE Fix + TPU Cover
    [TopCover_Cut_r3.stl, TopCover_ForTPU_r3.step, TopCover_ForTPU_r3.stl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]
2024-02-18 Whoops forgot to orientate the parts
    [TopCover_Cut_r3.stl, TopCover_ForTPU_r3.stl, TopCover_r3.stl]
2024-03-06 Add version for PapLite R3
    [Frank2 PapLite R3 Mount.stl]
2024-03-06 R3 mount image
2024-03-06 R3 mount
2024-04-29 r3.1 Update
    [2x_Idler_Pulley_F623_r3.1.stl, 2x_Idler_Pulley_r3.1.stl, 36mm_SIde_Spacer.stl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]
2024-04-30 Pulley Tolerance Fix
    [2x_Idler_Pulley_F623_r3.1.stl, 2x_Idler_Pulley_r3.1.stl]
2024-05-23 HGX 2.0 + TBG
    [BaseLower.stl, BaseLower_LGX_Mounting.stl, BaseUpper.stl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]
2024-07-02 OG Pap CAD
2024-11-17 Filament Switch User Mod
    [TopCover Dual Sensor Cut.stl, TopCover Dual Sensor.stl, TopCover Single Sensor Cut.stl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]
2025-01-20 Add A4T Extruder Adapters
    [a4t-papilio-adapter-cw2-tap.f3d, a4t-papilio-adapter-cw2-tap.stl, a4t-papilio-adapter-voron-logo-cw2-tap.f3d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]
2025-01-21 Create CAD
2025-01-21 Update CAD
2026-03-12 Papilio Legend files
    [Base.stl, EBB_36_PG7.stl, Faceplate_Accent.stl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]
2026-03-21 2.85mm Pulleys
2026-05-11 CAD Update
